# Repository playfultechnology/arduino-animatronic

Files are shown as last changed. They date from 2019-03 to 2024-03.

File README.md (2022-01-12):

# arduino-animatronic
This repository includes various resources for creating animatronic projects using an Arduino.

## 6-channel control using FlySky FS-i6 transmitter and FS-iA6 receiver
The <a href="https://www.banggood.com/custlink/vDKDONmsnv">FlySky FS-i6</a> is a popular and affordable 6-channel radio control transmitter unit often used for RC planes, drones etc., and is also suitable for real-time animatronic control. It has a total of 10 user inputs on the controller: 
 - 2x horizontal/vertical sticks
 - 3x 2-position toggles
 - 1x 3-position toggle
 - 2x rotary dials
Even though it has 10 inputs, out-of-the-box, you can only use 6 of those channels - the horizontal and vertical axes of the two sticks are always assigned to channels 1-4, while any two of the switches or dials can be assigned through the controller menu to channels 5-6.
Using the FS-IA6 receiver module which often comes supplied with the transmitter, you can access those 6 inputs by wiring the PWM signal output from each channel to a unique GPIO pin on an Arduino as follows:
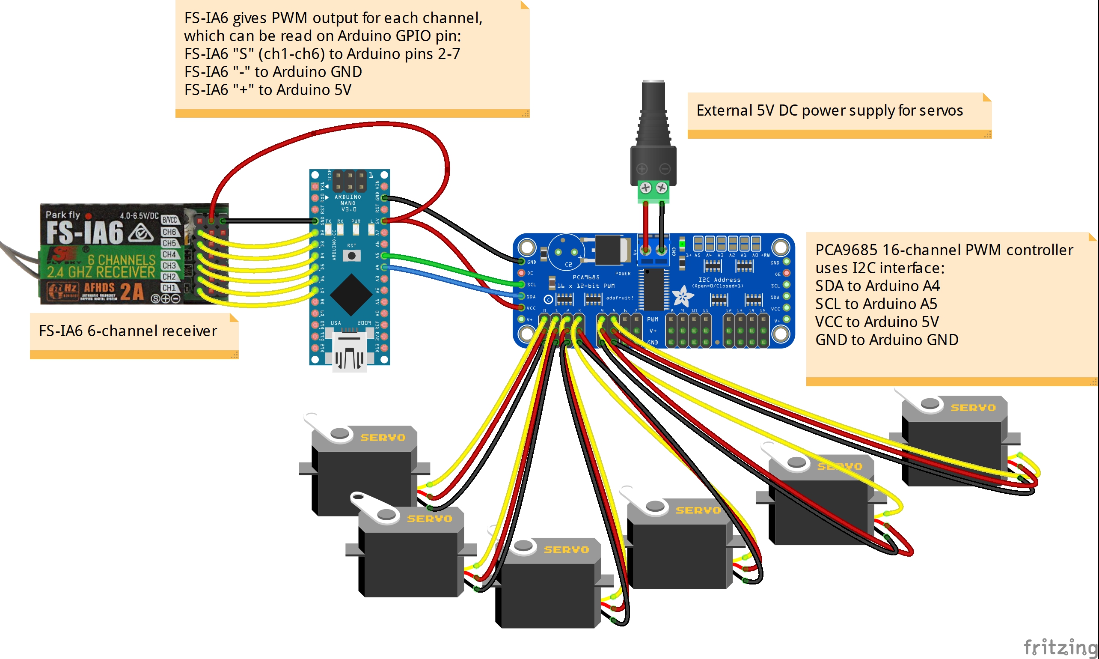
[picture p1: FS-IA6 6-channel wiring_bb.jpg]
PWM output from FS-IA6 wired to Arduino Wiring 6-channel PWM output from FS-IA6 receiver to Arduino Nano


## 10-channel control using upgraded FlySky FS-i6 transmitter and FS-iA6B receiver
The FS-iA6B is a newer receiver module than the FS-iA6, and is sometimes provided instead of the FS-iA6. While still being advertised as a 6-channel receiver and having only 6 PWM output pins, it includes support for the "iBus" protocol, which is a serial data interface that can carry up to 14-channels. Those extra channels makes the controller a very attractive choice for animatronic control. To make use of them, a few steps are required:

### Upgrade transmitter firmware ###
The FS-i6X controller already supports 10 channels, but to broadcast all 10 channels from the cheaper FS-i6 controller, we need to upgrade the firmware of the transmitter, which is normally done by connecting a separately-sold specialist USB data cable to the "trainer" socket on the back of the transmitter. However, since this is an Arduino project, you can use an Arduino to upgrade the firmware instead, wired as follows:
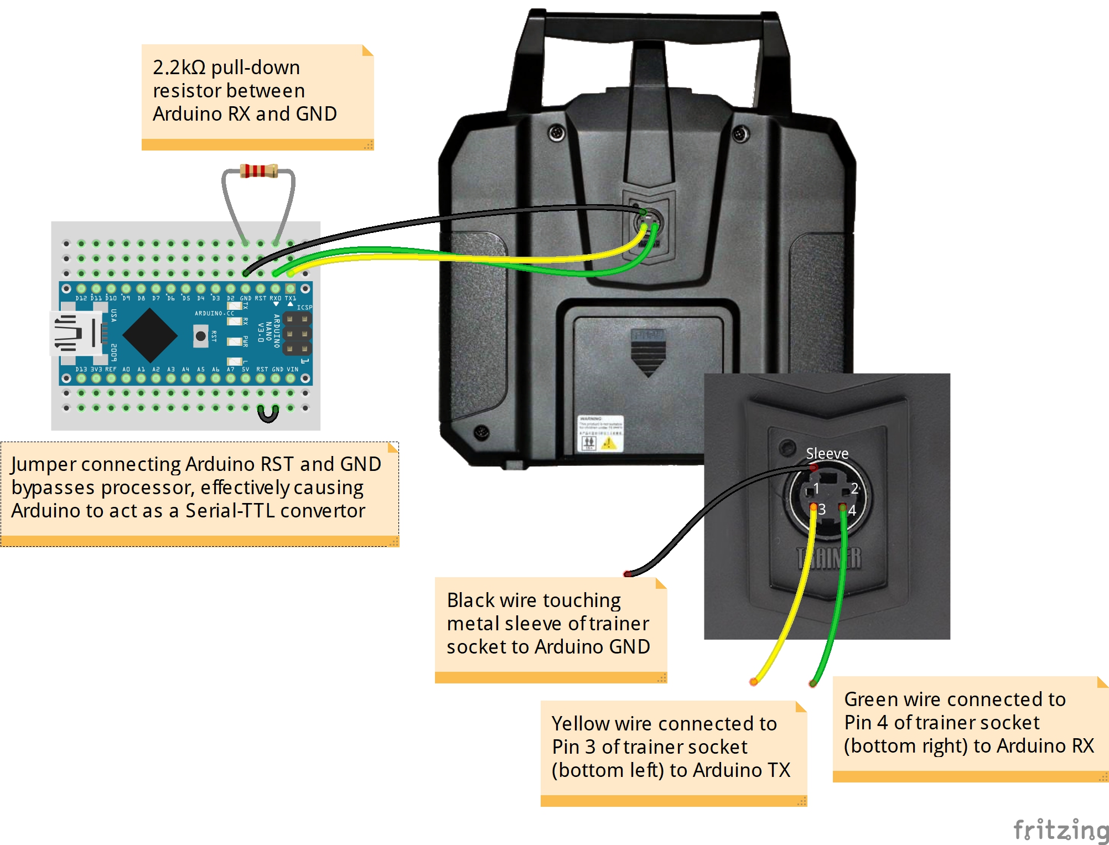
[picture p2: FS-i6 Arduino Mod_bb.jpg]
Flashing upgraded firmware using Arduino Nano Using an Arduino Nano to flash firmware to FlySky FS-i6 transmitter

Then, run <a href="https://github.com/benb0jangles/FlySky-i6-Mod-/tree/master/10ch%20Mod%20i6%20Updater/10ch_MOD_i6_Programmer_V1_5">this updater program</a> to flash new firmware to the transmitter, allowing all the face controls to be assigned to channels.

### Wiring via iBus interface ###

#### Using software serial on an Arduino Nano (5V) ####
The iBus interface uses a 115,200 baud serial connection. My initial build used Paul Stoffregen's excellent AltSoftSerial library to emulate this serial connection on GPIO pin 8 of an Arduino Nano: 
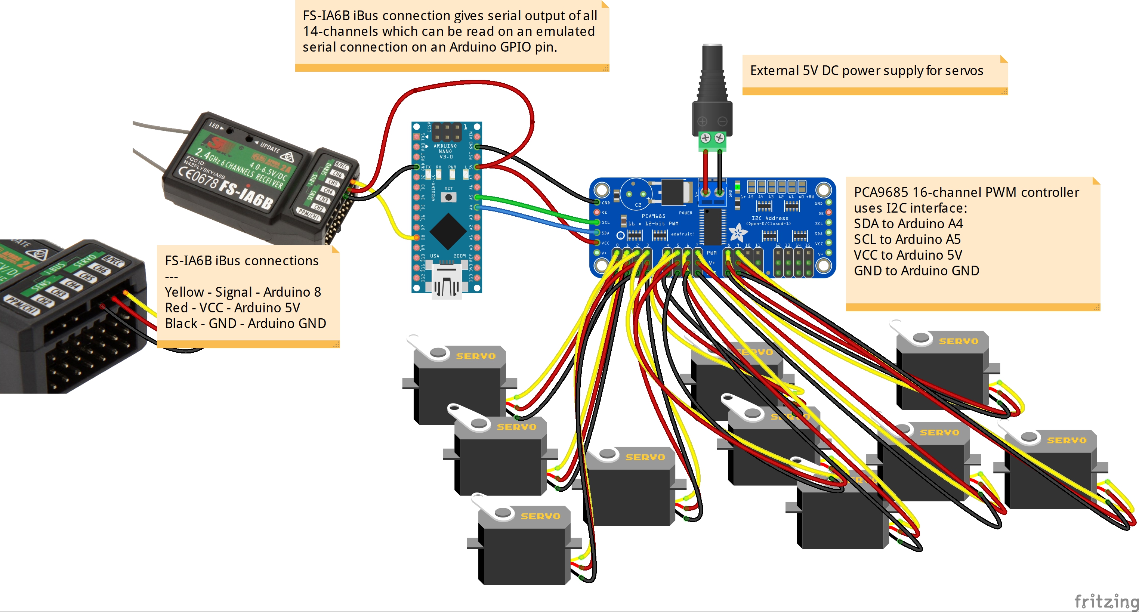
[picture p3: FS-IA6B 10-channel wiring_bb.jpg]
iBus output from FS-IA6B wired to Arduino Wiring 6-channel iBus output from FS-IA6B receiver to Arduino Nano


#### Using hardware serial on an ESP32 (3.3V) ####
I noticed after a while that the Arduino in the setup would occasionally crash, I suspect as a result of a buffer overrun with the emulation not being able to handle the 115,200 baud rate required by the iBus connection. A better solution is therefore to use a board with a dedicated hardware UART, such as an Arduino MEGA, or an ESP32. The PCA9685 can operate at 3.3V logic just fine so, since the ESP32 is the more capable board, I opted to adopt that approach instead:
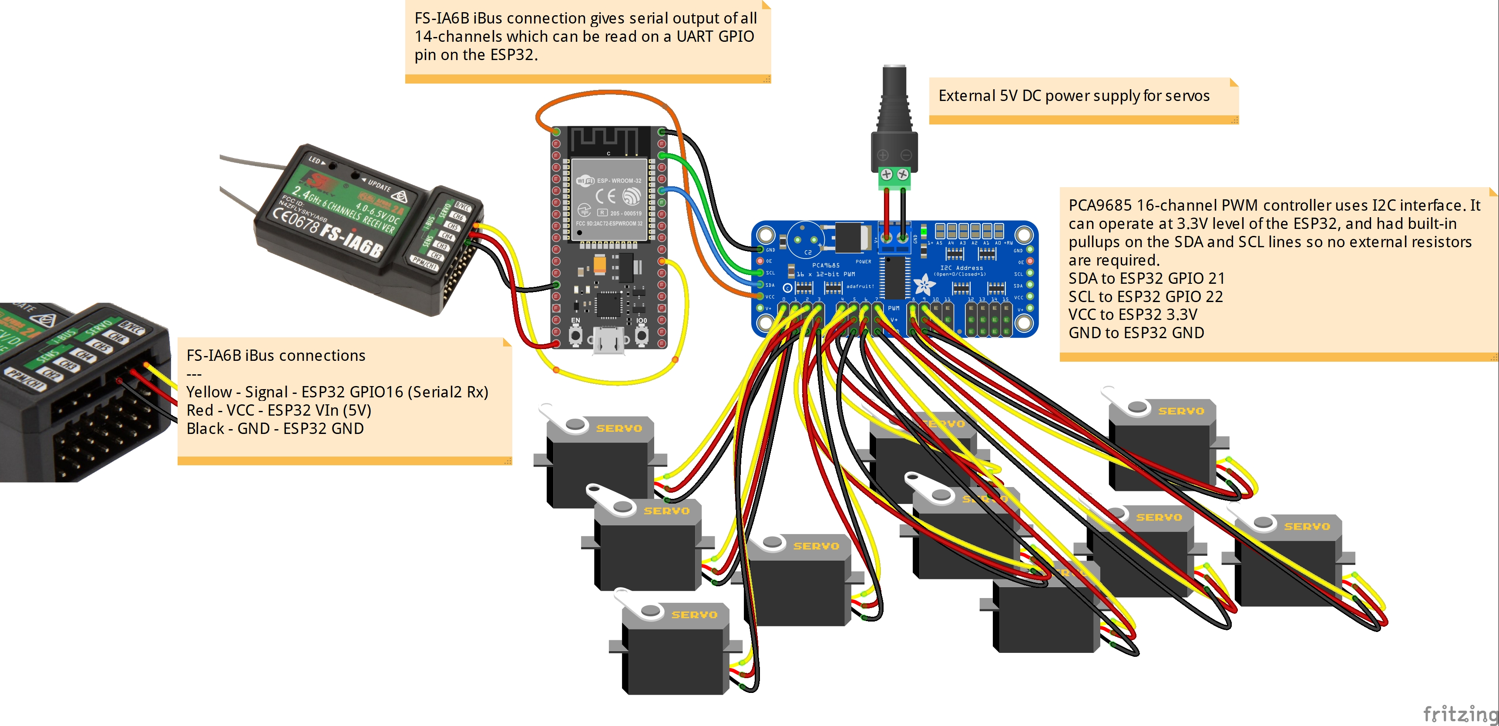
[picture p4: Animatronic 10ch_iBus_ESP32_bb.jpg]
iBus output from FS-IA6B wired to ESP32 Wiring 6-channel iBus output from FS-IA6B receiver to ESP32


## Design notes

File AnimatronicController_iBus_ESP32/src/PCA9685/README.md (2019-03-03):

# PCA9685-Arduino
Arduino Library for the PCA9685 16-Channel PWM Driver Module.

**PCA9685-Arduino - Version 1.2.10**

Library to control a PCA9685 16-channel PWM driver module from an Arduino board.  
Licensed under the copy-left GNU GPL v3 license.

Created by Kasper Skårhøj, August 3rd, 2012.  
Forked by Vitska, June 18th, 2016.  
Forked by NachtRaveVL, July 29th, 2016.

This library allows communication with boards running a PCA6985 16-channel PWM driver module. It supports a wide range of available functionality, from setting the output PWM frequecy, allowing multi-device proxy addressing, and provides an assistant class for working with Servos.

The datasheet for the IC is available from <http://www.nxp.com/documents/data_sheet/PCA9685.pdf>.

## Library Setup

There are several defines inside of the library's header file that allows for more fine-tuned control.

```Arduino
// Uncomment this define to enable use of the software i2c library (min 4MHz+ processor required).
//#define PCA9685_ENABLE_SOFTWARE_I2C     1   // http://playground.arduino.cc/Main/SoftwareI2CLibrary

// Uncomment this define if wanting to exclude extended functionality from compilation.
//#define PCA9685_EXCLUDE_EXT_FUNC        1

// Uncomment this define if wanting to exclude ServoEvaluator assistant from compilation.
//#define PCA9685_EXCLUDE_SERVO_EVAL      1

// Uncomment this define to enable debug output.
//#define PCA9685_ENABLE_DEBUG_OUTPUT     1
```

## Servo Control Note

Many 180 degree controlled digital servos run on a 20ms pulse width (50Hz update frequency) based duty cycle, and do not utilize the entire pulse width for their -90/+90 degree control. Typically, 2.5% of the 20ms pulse width (0.5ms) is considered -90 degrees, and 12.5% of the 20ms pulse width (2.5ms) is considered +90 degrees. This roughly translates to raw PCA9685 PWM values of 102 and 512 (out of the 4096 value range) for -90 to +90 degree control, but may need to be adjusted to fit your specific servo (e.g. some I've tested run ~130 to ~525 for their -90/+90 degree control). Also be aware that driving some servos past their -90/+90 degrees of movement can cause a little plastic limiter pin to break off and get stuck inside of the gearing, which could potentially cause the servo to become jammed. See the PCA9685_ServoEvaluator class to assist with calculating PWM values from Servo angle values.

## Example Usage

Below are several examples of library usage.

### Simple Example
```Arduino
#include <Wire.h>
#include "PCA9685.h"

PCA9685 pwmController;                  // Library using default Wire and default linear phase balancing scheme

void setup() {
    Serial.begin(115200);

    Wire.begin();                       // Wire must be started first
    Wire.setClock(400000);              // Supported baud rates are 100kHz, 400kHz, and 1000kHz

    pwmController.resetDevices();       // Software resets all PCA9685 devices on Wire line

    pwmController.init(B000000);        // Address pins A5-A0 set to B000000
    pwmController.setPWMFrequency(100); // Default is 200Hz, supports 24Hz to 1526Hz

    pwmController.setChannelPWM(0, 128 << 4); // Set PWM to 128/255, but in 4096 land

    Serial.println(pwmController.getChannelPWM(0)); // Should output 2048, which is 128 << 4
}

```

### Batching Example

In this example, we randomly select PWM frequencies on all 12 outputs and allow them to drive for 5 seconds before changing them.

```Arduino
#include <Wire.h>
#include "PCA9685.h"

PCA9685 pwmController;                  // Library using default Wire and default linear phase balancing scheme

void setup() {
	Serial.begin(115200);

    Wire.begin();                       // Wire must be started first
    Wire.setClock(400000);              // Supported baud rates are 100kHz, 400kHz, and 1000kHz

    pwmController.resetDevices();       // Software resets all PCA9685 devices on Wire line

    pwmController.init(B010101);        // Address pins A5-A0 set to B010101
    pwmController.setPWMFrequency(500); // Default is 200Hz, supports 24Hz to 1526Hz

    randomSeed(analogRead(0));          // Use white noise for our randomness
}

void loop() {
    word pwms[12];
    pwms[0] = random(0, 4096);
    pwms[1] = random(0, 4096);
    pwms[2] = random(0, 4096);
    pwms[3] = random(0, 4096);
    pwms[4] = random(0, 4096);
    pwms[5] = random(0, 4096);
    pwms[6] = random(0, 4096);
    pwms[7] = random(0, 4096);
    pwms[8] = random(0, 4096);
    pwms[9] = random(0, 4096);
    pwms[10] = random(0, 4096);
    pwms[11] = random(0, 4096);
    pwmController.setChannelsPWM(0, 12, pwms);
    delay(5000);

    // Note: Only 7 channels can be written in one i2c transaction due to a
    // BUFFER_LENGTH limit of 32, so 12 channels will take two i2c transactions.
}

```

### Multi-Device Proxy Example

In this example, we use a special instance to control other modules attached to it via the ALL_CALL register.

```Arduino
#include <Wire.h>
#include "PCA9685.h"

PCA9685 pwmController1;                 // Library using default Wire and default linear phase balancing scheme
PCA9685 pwmController2;                 // Library using default Wire and default linear phase balancing scheme

PCA9685 pwmControllerAll;               // Not a real device, will act as a proxy to pwmController1 and pwmController2

void setup() {
    Serial.begin(115200);

    Wire.begin();                       // Wire must be started first
    Wire.setClock(400000);              // Supported baud rates are 100kHz, 400kHz, and 1000kHz

    pwmController1.resetDevices();      // Software resets all PCA9685 devices on Wire line (including pwmController2 in this case)

    pwmController1.init(B000000);       // Address pins A5-A0 set to B000000
    pwmController2.init(B000001);       // Address pins A5-A0 set to B000001

    pwmController1.setChannelOff(0);    // Turn channel 0 off
    pwmController2.setChannelOff(0);    // On both

    pwmController1.enableAllCallAddress(); // Default address of 0xE0
    pwmController2.enableAllCallAddress(); // Same default address

    pwmControllerAll.initAsProxyAddresser(); // Same default address of 0x0E as used in enable above

    pwmControllerAll.setChannelPWM(0, 4096); // Enables full on on both pwmController1 and pwmController2

    Serial.println(pwmController1.getChannelPWM(0)); // Should output 4096
    Serial.println(pwmController2.getChannelPWM(0)); // Should also output 4096

    // Note: Various parts of functionality of the proxy class instance are actually
    // disabled - typically anything that involves a read command being issued.
}

```

### Servo Evaluator Example

In this example, we utilize the ServoEvaluator class to assist with setting PWM frequencies when working with servos. We will be using Wire1, which is only available on boards with SDA1/SCL1 (Due, Zero, etc.) - change to Wire if Wire1 is unavailable.

```Arduino
#include <Wire.h>
#include "PCA9685.h"

PCA9685 pwmController(Wire1, PCA9685_PhaseBalancer_Weaved); // Library using Wire1 and weaved phase balancing scheme

// Linearly interpolates between standard 2.5%/12.5% phase length (102/512) for -90°/+90°
PCA9685_ServoEvaluator pwmServo1;

// Testing our second servo has found that -90° sits at 128, 0° at 324, and +90° at 526.
// Since 324 isn't precisely in the middle, a cubic spline will be used to smoothly
// interpolate PWM values, which will account for said discrepancy. Additionally, since
// 324 is closer to 128 than 526, there is less resolution in the -90° to 0° range, and
// more in the 0° to +90° range.
PCA9685_ServoEvaluator pwmServo2(128,324,526);

void setup() {
    Serial.begin(115200);

    Wire1.begin();                      // Wire must be started first
    Wire1.setClock(400000);             // Supported baud rates are 100kHz, 400kHz, and 1000kHz

    pwmController.resetDevices();       // Software resets all PCA9685 devices on Wire line

    pwmController.init(B000000);        // Address pins A5-A0 set to B000000
    pwmController.setPWMFrequency(50);  // 50Hz provides 20ms standard servo phase length

    pwmController.setChannelPWM(0, pwmServo1.pwmForAngle(-90));
    Serial.println(pwmController.getChannelPWM(0)); // Should output 102 for -90°

    // Showing linearity for midpoint, 205 away from both -90° and 90°
    Serial.println(pwmServo1.pwmForAngle(0));   // Should output 307 for 0°

    pwmController.setChannelPWM(0, pwmServo1.pwmForAngle(90));
    Serial.println(pwmController.getChannelPWM(0)); // Should output 512 for +90°

    pwmController.setChannelPWM(1, pwmServo2.pwmForAngle(-90));
    Serial.println(pwmController.getChannelPWM(1)); // Should output 128 for -90°

    // Showing less resolution in the -90° to 0° range
    Serial.println(pwmServo2.pwmForAngle(-45)); // Should output 225 for -45°, 97 away from -90°

    pwmController.setChannelPWM(1, pwmServo2.pwmForAngle(0));
    Serial.println(pwmController.getChannelPWM(1)); // Should output 324 for 0°

    // Showing more resolution in the 0° to +90° range
    Serial.println(pwmServo2.pwmForAngle(45));  // Should output 424 for +45°, 102 away from +90°

    pwmController.setChannelPWM(1, pwmServo2.pwmForAngle(90));
    Serial.println(pwmController.getChannelPWM(1)); // Should output 526 for +90°
}

```

### Software I2C Example

In this example, we utilize the software I2C functionality for chips that do not have a hardware I2C bus. We must uncomment the PCA9685_ENABLE_SOFTWARE_I2C define in the libraries main header file for software I2C mode to be enabled.

In PCA9685.h:
```Arduino
// Uncomment this define to enable use of the software i2c library (min 4MHz+ processor required).
#define PCA9685_ENABLE_SOFTWARE_I2C     1   // http://playground.arduino.cc/Main/SoftwareI2CLibrary
```

In main sketch:
```Arduino
#include "PCA9685.h"

#define SCL_PIN 2                       // Setup defines are written before library include
#define SCL_PORT PORTD 
#define SDA_PIN 0 
#define SDA_PORT PORTC 

#if F_CPU >= 16000000
#define I2C_FASTMODE 1                  // Running a 16MHz processor allows us to use I2C fast mode
#endif

#include "SoftI2CMaster.h"              // Include must come after setup defines

PCA9685 pwmController;                  // Library using default linear phase balancing scheme

void setup() {
	Serial.begin(115200);

    i2c_init();                         // Software I2C must be started first

    pwmController.resetDevices();       // Software resets all PCA9685 devices on software I2C line

    pwmController.init(B000000);        // Address pins A5-A0 set to B000000

    pwmController.setChannelPWM(0, 2048); // Should see a 50% duty cycle along the 5ms phase width
}

```

## Module Info

If one uncomments the PCA9685_ENABLE_DEBUG_OUTPUT define in the libraries main header file (thus enabling debug output) the printModuleInfo() method becomes available, which will display information about the module itself, including initalized states, register values, current settings, etc. All calls being made will display internal debug information about the structure of the call itself. An example of this output is shown here:

In PCA9685.h:
```Arduino
// Uncomment this define to enable debug output.
#define PCA9685_ENABLE_DEBUG_OUTPUT     1
```

In main sketch:
```Arduino
#include <Wire.h>
#include "PCA9685.h"

PCA9685 pwmController;

void setup() {
    Serial.begin(115200);

    Wire.begin();                       // Wire must be started first
    Wire.setClock(400000);              // Supported baud rates are 100kHz, 400kHz, and 1000kHz

    pwmController.printModuleInfo();
}

```

In serial monitor:
```
  ~~~ PCA9685 Module Info ~~~

i2c Address:
0x40

Phase Balancer:
PCA9685_PhaseBalancer_Weaved

Proxy Addresser:
false

Mode1 Register:
  PCA9685::readRegister regAddress: 0x0
    PCA9685::readRegister retVal: 0x20
0x20, Bitset: PCA9685_MODE_AUTOINC

Mode2 Register:
  PCA9685::readRegister regAddress: 0x1
    PCA9685::readRegister retVal: 0xC
0xC, Bitset: PCA9685_MODE_OUTPUT_ONACK PCA9685_MODE_OUTPUT_TPOLE

SubAddress1 Register:
  PCA9685::readRegister regAddress: 0x2
    PCA9685::readRegister retVal: 0xE2
0xE2

SubAddress2 Register:
  PCA9685::readRegister regAddress: 0x3
    PCA9685::readRegister retVal: 0xE4
0xE4

SubAddress3 Register:
  PCA9685::readRegister regAddress: 0x4
    PCA9685::readRegister retVal: 0xE8
0xE8

AllCall Register:
  PCA9685::readRegister regAddress: 0x5
    PCA9685::readRegister retVal: 0xE0
0xE0

```

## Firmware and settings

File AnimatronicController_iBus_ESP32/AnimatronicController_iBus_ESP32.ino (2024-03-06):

/**
 * Realtime Arduino Animatronic Controller (10 channel, iBus version)
 * 
 * This Arduino script reads serial data from the iBus interface of a RC receiver such as the Flysky FS-iA6B,
 * It then applies various logic to these inputs based on a chosen animatronic model (tentacle, eye, etc.) and assigns corresponding
 * positions of an array of servo motors via a PCA9685 PWM controller.
 */

// DEFINES
// Hardware UART port to use for iBus interface
#define iBusSerial Serial2

// INCLUDES
// Wire library used for I2C communication
#include <Wire.h>
// PCA9685 16-channel PWM controller
// See: https://github.com/NachtRaveVL/PCA9685-Arduino
#include "src/PCA9685/PCA9685.h"
// FlySky iBus interface adapted from https://gitlab.com/timwilkinson/FlySkyIBus
#include "src/FlySkyIBus/FlySkyIBus.h"
// For OLED Display
#include <lcdgfx.h>

// CONSTANTS
// How many channels to read from the iBus packet (max 14)
const int numInputChannels = 10;
// This is the number of output channels (i.e. servo motors) to be controlled by the script
// Note that the logic applied by the script means that there is not a 1:1 mapping between inputs and outputs
// so this number can be greater or less than the number of inputs 
const byte numOutputChannels = 10;
// Define some common animatronic behaviour types
enum Behaviour {
  Passthrough, // Pass all inputs unchanged to corresponding numbered outputs
  SimpleTentacle, // X/Y tentacle movement only e.g. https://www.thingiverse.com/thing:6986
  WigglyTentacle, // X/Y tentacle with random wigggles added.
  DualTentacles, // 2x independent X/Y movement
  SimpleEye, // X movement of eye, Y movement of eyelids
  Eye,
};

// GLOBALS
// Instantiate an IBus object to process IBus data
FlySkyIBus iBus;
// Initialise the PWM controller which will send output to the servos
PCA9685 pwmController;
// Helper function to calculate pulse required for given angle
PCA9685_ServoEvaluator pwmServo;
// Define the behavior which we'd like the model to follow
Behaviour behaviour = Behaviour::Passthrough;
// Array of input channel values read from the iBus packet received from FS-iA6B
int channelInput[numInputChannels];
// Array of output channel values to send to PCA9685
int channelOutput[numOutputChannels];
// OLED display
DisplaySSD1306_128x64_I2C display(-1); 

void setup() {
  // Software serial connection to the FS-IA6B receiver 
  iBusSerial.begin(115200);
  // Attach the IBus object to the ibusSerial interface
  iBus.begin(iBusSerial);

  // Initialise I2C interface used for the PCA9685 PWM controller
  Wire.begin();
  // Supported baud rates are 100kHz, 400kHz, and 1000kHz
  //Wire.setClock(400000);
  // Initialise PCA9685
  pwmController.resetDevices();
  pwmController.init();
  // 50Hz provides 20ms standard servo phase length
  pwmController.setPWMFrequency(50);

  // Hardware USB serial connection to the Arduino IDE monitor
  Serial.begin(115200);
  Serial.println("Ready!");

  /* Select the font to use with menu and all font functions */
  display.setFixedFont( ssd1306xled_font6x8 );
  display.begin();
  display.clear();
  display.printFixed(0,  0, "Animatronic Control", STYLE_NORMAL);
 
}

void loop() {
  // iBus data is sent is discrete packets. We'll call IBus.loop() on every
  // frame to check whether a new packet has been received. If so, it will return true.
  if(iBus.loop()) {

    for(int i=0; i<numInputChannels; i++) {
      channelInput[i] = iBus.readChannel(i);
      Serial.print(channelInput[i]);
      Serial.print(",");
    }
    Serial.println("");

    // Now perform whatever logic is necessary to convert from the array of input channels
    // into the array of output values
    ApplyLogic();
  
    // Now, send the output values to the PWM servo controller
    for(int i=0; i<numOutputChannels; i++) {
      pwmController.setChannelPWM(i, channelOutput[i]);
    }

    char s[21];
    snprintf(s, 21, "Ch0:%u   Ch1:%u", channelInput[0], channelInput[1]);
    display.printFixed(0,  16, s, STYLE_NORMAL);
    snprintf(s, 21, "Ch2:%u   Ch3:%u", channelInput[2], channelInput[3]);
    display.printFixed(0,  24, s, STYLE_NORMAL);
    snprintf(s, 21, "Ch4:%u   Ch5:%u", channelInput[4], channelInput[5]);
    display.printFixed(0,  32, s, STYLE_NORMAL);
    snprintf(s, 21, "Ch6:%u   Ch7:%u", channelInput[6], channelInput[7]);
    display.printFixed(0,  40, s, STYLE_NORMAL);
    snprintf(s, 21, "Ch8:%u   Ch9:%u", channelInput[8], channelInput[9]);
    display.printFixed(0,  48, s, STYLE_NORMAL);
  }
}

// This function processes inputs and calculates the appropriate outputs
// based on the selected model
void ApplyLogic(){
  // Behaviour depends on chosen model
  switch(behaviour) {
  
    case Behaviour::Passthrough: {
      int n = min(numInputChannels, numOutputChannels);
      for(int i=0; i<n; i++){
        if(channelInput[i] > 995 && channelInput[i] < 2000) {
          int X = map(channelInput[i], 1000, 2000, -90, 90);
          channelOutput[i] = pwmServo.pwmForAngle(X);
        }
      }
    }
    break;

    case Behaviour::SimpleTentacle: {
      // Calculate movement in X axis
      int X = 0;
      // The ON period of almost all RC pulses range from 1000us to 2000us.
      // We'll remap this to an angle from -45 to +45
      if(channelInput[0] > 995 && channelInput[0] < 2000) { 
        X = map(channelInput[0], 1000, 2000, -90, 90);
      }
      // Calculate PWM corresponding to desired angle and assign to output channel 0
      channelOutput[0] = pwmServo.pwmForAngle(X);

      // Calculate movement in the Y axis
      int Y = 0;
      if(channelInput[1] > 995 && channelInput[1] < 2000) { 
        Y = map(channelInput[1], 1000, 2000, -90, 90);
      }
      // Calculate PWM corresponding to desired angle and assign to output channel 1
      channelOutput[1] = pwmServo.pwmForAngle(Y);
      }
      break;

    case Behaviour::WigglyTentacle: {
      // Calculate movement in X axis
      int X = 0;
      // The ON period of almost all RC pulses range from 1000us to 2000us.
      // We'll remap this to an angle from -45 to +45
      if(channelInput[0] > 995 && channelInput[0] < 2000) { 
        X = map(channelInput[0], 1000, 2000, -90, 90);
      }
      // Calculate additional periodic wiggly offset
      X += 6 * sin(millis() * 0.005);
      // Calculate PWM corresponding to desired angle and assign to output channel 0
      channelOutput[0] = pwmServo.pwmForAngle(X);

      // Calculate movement in Y axis
      int Y = 0;
      if(channelInput[1] > 995 && channelInput[1] < 2000) { 
        Y = map(channelInput[1], 1000, 2000, -90, 90);
      }
      // Calculate additional periodic wiggly offset
      Y += 5 * cos(millis() * 0.0051);

      // Calculate PWM corresponding to desired angle and assign to output channel 1
      channelOutput[1] = pwmServo.pwmForAngle(Y);
      }
      break;

    case Behaviour::DualTentacles: {
      int X1 = 0;
      // The ON period of almost all RC pulses range from 1000us to 2000us.
      // We'll remap this to an angle from -90 to +90
      if(channelInput[0] > 995 && channelInput[0] < 2000) { 
        X1 = map(channelInput[0], 1000, 2000, -90, 90);
      }
      // Calculate PWM corresponding to desired angle and assign to output channel 0
      channelOutput[0] = pwmServo.pwmForAngle(X1);

      int Y1 = 0;
      if(channelInput[1] > 995 && channelInput[1] < 2000) { 
        Y1 = map(channelInput[1], 1000, 2000, -90, 90);
      }
      // Calculate PWM corresponding to desired angle and assign to output channel 1
      channelOutput[1] = pwmServo.pwmForAngle(Y1);

      int X2 = 0;
      // The ON period of almost all RC pulses range from 1000us to 2000us.
      // We'll remap this to an angle from -45 to +45
      if(channelInput[0] > 995 && channelInput[2] < 2000) { 
        X2 = map(channelInput[0], 1000, 2000, -90, 90);
      }
      // Calculate PWM corresponding to desired angle and assign to output channel 2
      channelOutput[2] = pwmServo.pwmForAngle(X2);

      int Y2 = 0;
      if(channelInput[1] > 995 && channelInput[3] < 2000) { 
        Y2 = map(channelInput[1], 1000, 2000, -90, 90);
      }
      // Calculate PWM corresponding to desired angle and assign to output channel 3
      channelOutput[3 ] = pwmServo.pwmForAngle(Y2);
      }
      break;

    case Behaviour::SimpleEye: {
      // EYE LEFT/RIGHT
      int eyeX = 0;
      if(channelInput[0] > 995 && channelInput[0] < 2000) { 
        // The ON period of almost all RC pulses range from 1000us to 2000us.
        // We'll remap this to an angle from -90 to +90
        eyeX = map(channelInput[0], 1000, 2000, -90, 90);
      }
      // Calculate PWM corresponding to desired angle and assign to output channel 0
      channelOutput[0] = pwmServo.pwmForAngle(eyeX);

      // EYELID UP/DOWN
      int eyelidY = 0;
      if(channelInput[1] > 995 && channelInput[1] < 2000) { 
        eyelidY = map(channelInput[1], 1000, 2000, -45, 90);
      }
      // CHANCE OF RANDOM BLINK
      static unsigned long nextBlinkTime;
      if(millis() > nextBlinkTime && millis() < nextBlinkTime + 200) {
        eyelidY = -45;
      }
      else if(millis() > nextBlinkTime + 200) {
        nextBlinkTime += random(5000, 8000);
      }
      // Calculate PWM corresponding to desired angle and assign to output channel 1
      channelOutput[1] = pwmServo.pwmForAngle(eyelidY);
      }
      break;

    case Behaviour::Eye: {
     // The ON period of almost all RC pulses range from 1000us to 2000us.
      // We'll remap this to an angle from -45 to +45
      int eyeX = map(channelInput[0], 1000, 2000, -30, 30);
      channelOutput[0] = pwmServo.pwmForAngle(eyeX);
      int eyeY = map(channelInput[1], 1000, 2000, -25, 25);
      channelOutput[1] = pwmServo.pwmForAngle(eyeY);
    
      int eyesWideOpen = map(channelInput[2], 1000, 2000, -10, 10);
      int topEyelid = eyesWideOpen + eyeY / 2;
      channelOutput[2] = pwmServo.pwmForAngle(topEyelid);
      int bottomEyelid = eyesWideOpen - eyeY / 2;
      channelOutput[3] = pwmServo.pwmForAngle(bottomEyelid);
      }
      break;
    
    default: 
      break;
  }
}

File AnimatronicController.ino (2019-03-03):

// Arduino pins are grouped into 3 "ports" that share a pin change interrupt
// Set the PORTS_TO_USE value to specify which group of pins to use to read the RC ahnnel inputs
// PORTS_TO_USE  1 for pins D8-D13
// PORTS_TO_USE 2 for pins A0-A5
// PORTS_TO_USE 3 for pins D0-D7
#define PORTS_TO_USE 3

//INCLUDES
// Wire library used for I2C communication
#include <Wire.h>
// PCA9685 16-channel PWM controller
// https://github.com/NachtRaveVL/PCA9685-Arduino
#include "src/PCA9685/PCA9685.h"
// Helper library for reading PPM signals from RC receiver
// https://github.com/timoxd7/FastRCReader
#include "src/FastRCReader/FastRCReader.h"

// CONSTANTS
// I'm using a FS-IA6 6-channel receiver
const int numInputChannels = 6;
// Each channel will be assigned a unique pin in the range defined by PORTS_TO_USE
uint8_t channelPins[numInputChannels] = {7,6,5,4,3,2};
const byte numOutputChannels = 2;

enum Behaviour {
  SimpleTentacle, // X/Y tentacle movement only e.g. https://www.thingiverse.com/thing:6986
  WigglyTentacle, // X/Y tentacle with random wigggles added.
  SimpleEye, // X movement of eye, Y movement of eyelids
  Eye,
};

// GLOBALS
PCA9685 pwmController;
PCA9685_ServoEvaluator pwmServo;
FastRCReader RC;
Behaviour behaviour = Behaviour::SimpleEye;

// Array of current channel input values
int channelInput[numInputChannels];
int channelOutput[numOutputChannels];

// This function processes inputs and clacualted the appropriate outputs.
// It applies different behaviour for, say, a tentacle or a pair of eyes
void ApplyLogic(){

  switch(behaviour) {

    case Behaviour::SimpleTentacle: 
    {
      int X = 0;
      // The ON period of almost all RC pulses range from 1000us to 2000us.
      // We'll remap this to an angle from -45 to +45
      if(channelInput[0] > 995 && channelInput[0] < 2000) { 
        X = map(channelInput[0], 1000, 2000, -90, 90);
      }
      //Serial.println(X);
      channelOutput[0] = pwmServo.pwmForAngle(X);

      int Y = 0;
      if(channelInput[1] > 995 && channelInput[1] < 2000) { 
        Y = map(channelInput[1], 1000, 2000, -90, 90);
      }
      channelOutput[1] = pwmServo.pwmForAngle(Y);
    }
      break;

    case Behaviour::WigglyTentacle: 
    {
      int X = 0;
      // The ON period of almost all RC pulses range from 1000us to 2000us.
      // We'll remap this to an angle from -45 to +45
      if(channelInput[0] > 995 && channelInput[0] < 2000) { 
        X = map(channelInput[0], 1000, 2000, -90, 90);
      }
      float theta = millis() * 0.005;
      X += 6 * sin(theta);   
      channelOutput[0] = pwmServo.pwmForAngle(X);

      int Y = 0;
      if(channelInput[1] > 995 && channelInput[1] < 2000) { 
        Y = map(channelInput[1], 1000, 2000, -90, 90);
      }
      Y += 5 * cos(theta * 1.01);
      channelOutput[1] = pwmServo.pwmForAngle(Y);
    }
      break;

    case Behaviour::SimpleEye: 
    {
      // EYE LEFT/RIGHT
      int eyeX = 0;
      if(channelInput[0] > 995 && channelInput[0] < 2000) { 
        // The ON period of almost all RC pulses range from 1000us to 2000us.
        // We'll remap this to an angle from -45 to +45
        eyeX = map(channelInput[0], 1000, 2000, -90, 90);
      }
      channelOutput[0] = pwmServo.pwmForAngle(eyeX);

      // EYELID UP/DOWN
      int eyelidY = 0;
      if(channelInput[1] > 995 && channelInput[1] < 2000) { 
        eyelidY = map(channelInput[1], 1000, 2000, -45, 90);
      }
      // CHANCE OF RANDOM BLINK
      static unsigned long nextBlinkTime;
      if(millis() > nextBlinkTime && millis() < nextBlinkTime + 200) {
        eyelidY = -45;
      }
      else if(millis() > nextBlinkTime + 200) {
        nextBlinkTime += random(5000, 8000);
      }
      channelOutput[1] = pwmServo.pwmForAngle(eyelidY);
    }
    break;

    case Behaviour::Eye: 
    {
     // The ON period of almost all RC pulses range from 1000us to 2000us.
      // We'll remap this to an angle from -45 to +45
      int eyeX = map(channelInput[0], 1000, 2000, -30, 30);
      channelOutput[0] = pwmServo.pwmForAngle(eyeX);
      int eyeY = map(channelInput[1], 1000, 2000, -25, 25);
      channelOutput[1] = pwmServo.pwmForAngle(eyeY);
    
      int eyesWideOpen = map(channelInput[2], 1000, 2000, -10, 10);
      int topEyelid = eyesWideOpen + eyeY / 2;
      channelOutput[2] = pwmServo.pwmForAngle(topEyelid);
      int bottomEyelid = eyesWideOpen - eyeY / 2;
      channelOutput[3] = pwmServo.pwmForAngle(bottomEyelid);
    }
    break;
    
    default: 
      break;
  }
}


void setup() {
  // Initialise the serial connection
  Serial.begin(9600);

  RC.begin();
  RC.addChannel(channelPins, numInputChannels);

  // Initialise I2C interface used 
  Wire.begin();
  // Supported baud rates are 100kHz, 400kHz, and 1000kHz
  Wire.setClock(400000);

    pwmController.resetDevices();       // Software resets all PCA9685 devices on Wire line

    pwmController.init();        // Address pins A5-A0 set to B000000
    pwmController.setPWMFrequency(50);  // 50Hz provides 20ms standard servo phase length

//    pwmController.setChannelPWM(0, 128 << 4); // Set PWM to 128/255, but in 4096 land

}

void loop() {
  // Read all the current channel input values into the input array
  for(int i=0; i<numInputChannels; i++) {
    channelInput[i] = RC.getFreq(channelPins[i]);
      Serial.print(channelInput[i]);
      Serial.print(",");
  }
  Serial.println();

  
  // Now perform whatever logic is necessary
  ApplyLogic();
  
  for(int i=0; i<numOutputChannels; i++) {
    pwmController.setChannelPWM(i, channelOutput[i]);
  }
}

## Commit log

2019-09-03 Create FS-i6 Arduino Mod_bb.jpg
2019-09-04 Create FS-IA6 6-channel wiring_bb.jpg
2019-09-04 Create FS-IA6B 10-channel wiring_bb.jpg
2019-09-04 PWM v1.0
2019-09-04 Added Fritzing projects
    [Animatronic 10ch_iBus.fzz, Animatronic_6ch_PWM.fzz, FS-i6 Arduino FIrmware Mod.fzz]
2022-01-10 Added firmware mod to increase transmitter to 10 channels
    [Animatronic 10ch_iBus.fzz]
2022-01-10 ESP32 support
    Added wiring diagram for ESP32 and I2C buffer length fix for ESP32
    [Animatronic 10ch_iBus_ESP32.fzz]
2022-01-10 Added ESP32 version based on Hardware UART
    SoftwareSerial emulation was struggling to maintain 115200 required baud rate to iBus interface, so switched to using dedicated hardware serial on ESP32 instead.
